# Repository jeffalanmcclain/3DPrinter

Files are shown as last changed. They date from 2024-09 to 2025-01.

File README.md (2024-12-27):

The purpose of this GIT is to serve as a CONFIG file backup for my various 3D Printers and to document the MODs I've made to them.
# [Config files](Config/README.md)
- [Flash Forge Adventurer 5M Pro](Config/FlashForge%20Adventurer%205MPro/)
- [Siboor AWD Trident 350mm](Config/Siboor%20AWD%20Trident%20350mm/)
# [Builds/Mods](Hardware/)
- Flash Forge 5MPro
- [Siboor AWD CNC Trident 350mm](Hardware/Siboor%20AWD%20Trident%20350mm/)
# [Documents/Checklists](Documents/readme.md)

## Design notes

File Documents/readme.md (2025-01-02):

# List of things to do
- [x]Install umbilical
- [x]Fix adapter cable GND/Vin swapped
- [x]Make up new umbilical from frame to toolhead
- [x]Look into X-axis resonance
 - [x]Is it affected by putting printer on hardwood floor instead of shakey card table...some, but not the double issue.
 - [x]Need better cable swing support?  Don't think so.
 - [x]Get both EBB36 adxl345 and Carto working to compare.  Now I have even MORE questions...lol.
- [x]Design webcam mount integrated into Apex-eng corner bracket
 - [x]print it and test it
- [x]Rerun Voron Calibration Cube
- [x]Rewrite entire HOME routine to force safer X/Y order operation (and skip if not needed)
- [x]Fix/Improve the feed between Extruder and HE on XOL toolhead
  - [x]Order Stainless 4mm OD x 2mm ID tube
  - [x]Install in XOL
- [x]Restructure entire congig section into directories and move some things under manta.cfg
- [x]Document everything on GIT
  - [x]Initial refactored GIT structure
  - [x]Samba share on CM4
  - [x]Sync GIT to samba share
  - [x]Sym-link Siboor config in GIT structure to ~/printer_data/config
  - [x]Pull-sync to printer
  - [x]Ensure restart works
  - [x]Update links/images formatting into better table structure
- [x]Update Internal Spoolholder STL to have recessed spring/bolts
- [x]Work on reverse tunnel proxy service to gain external access
- [x]Install Fluidd/Mainsail as docker on NAS
- [ ]Update Carto FW when available to fix Coil Frequency error
- [ ]Build StealthBurner
- [ ]Put endstop switch on Z-axis max?

# Debug Stuff for TTC and canbus traffic

- To check for errors on canbus (non-invasive)

```
candump can0,0~0,#FFFFFFFF
```

- To generate canbus loading (kills klipper, if it is running)

```
cangen -e -g 0.12 can0
```

- To watch for traffic on the canbus

```
watch -n 1 -d "ip -details -statistics link show can0"
watch -n 1 "tc -s qdisc show dev can0"
```

- To watch load on the canbus (as percentage %)

```
canbusload can0@1000000 -b -c
```

- To graph klipper.log

```
~/klipper/scripts/graphstats.py /tmp/klippy.log -o loadgraph_host.png
```

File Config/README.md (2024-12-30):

# Klipper Configs
## Methodology
Overall, I work hard to segregate things out into their individual constituant components.  Very much like Object Oriented programming, things should all be self contained inside their own entity.  This makes it (in theory) __very__ easy to remove something from your system and ONLY comment out that include file.  If you can not, then you have something wrong in your hierachy thinking.  I've done a LOT to try to enable this to function and NOT refer to other MCU pins that are NOT defined in your section.  It could be argued that some macros belong in more generalized areas, but if it deals with movement of the heads or moving the table/bed up/down, I believe THAT particular function belongs in `motion.cfg`.  
__All__ of the pin definitions for a given MCU should be in that area.  For example, there is an EBB36 MCU on the XOL toolhead.  All of the fans connected to that toolhead should be defined in there, of another file included from there like `xol_fans.cfg`.

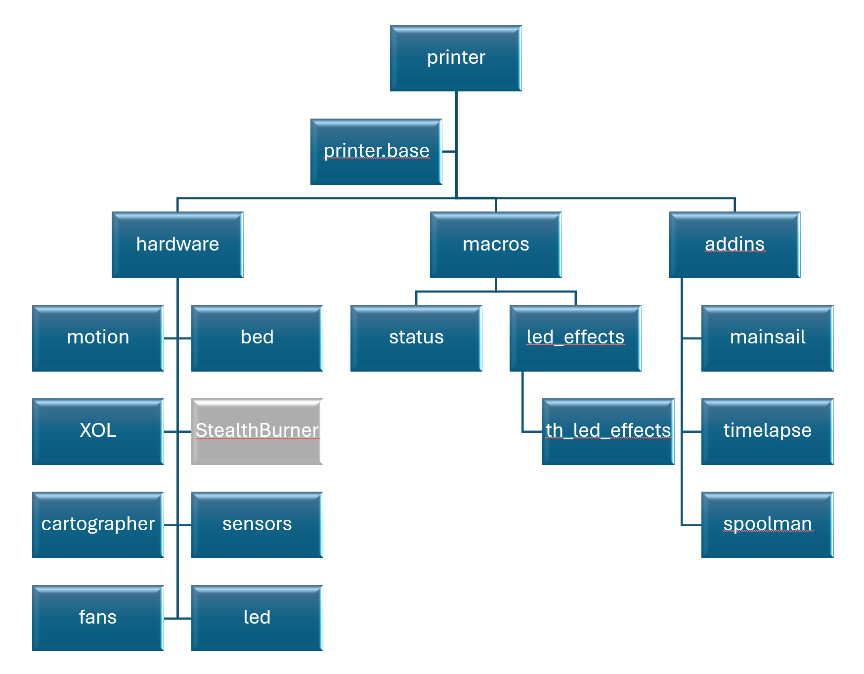
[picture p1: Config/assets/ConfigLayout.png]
Example Hierarchy of Config files


You could argue that putting toolhead fans in the `xol.cfg` breaks the idea of a "universal" fans location in the `fans.cfg` and probalby you'd be right (and even toolhead led's are in the xol.cfg, but the chamber led's are in their own led.cfg).  Technically, I should have made a `manta.cfg` under `hardware.cfg` and then put `motion.cfg` and `fans.cfg` and `bed.cfg` all below that, and you could then have fans and led below XOL as well to be more clear.  Here, each item in :red_circle:red:red_circle: has it's own MCU on the canbus.  

To that end, I have moved all my configs toward this later approach:

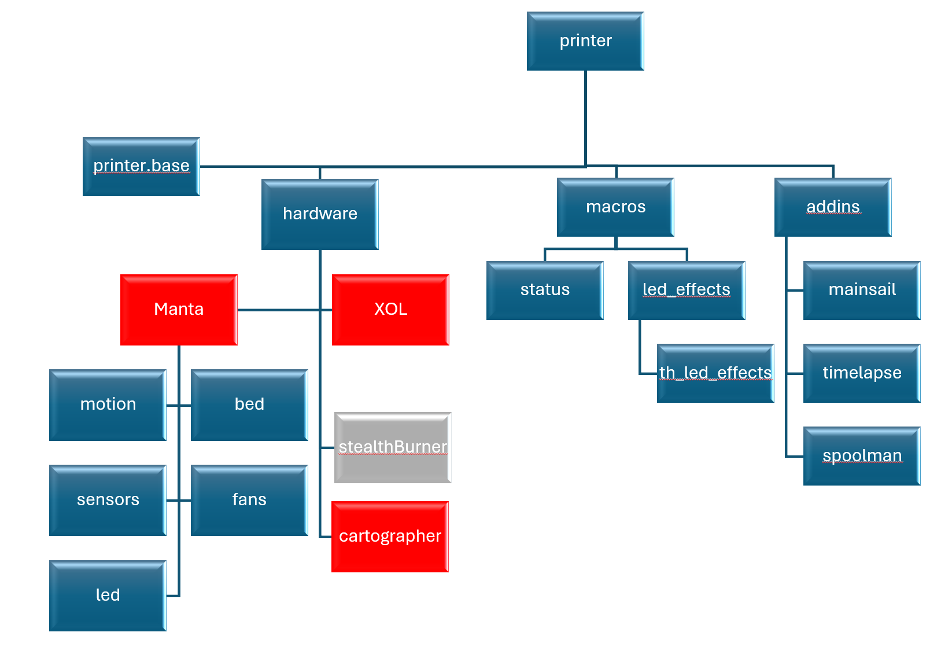
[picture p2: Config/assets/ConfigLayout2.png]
Alternate Example Hierarch


But as it stands now, to swap between StealthBurner and XOL toolhead, even with all the different toolhead MCU boards, IOs, different fans and pin defs and stuff, it is as simple as comment __OUT__ `XOL.cfg` and uncomment `stealthburner.cfg` in `hardware.cfg` include list.  Or really, to power up the printer and have it functional, without the TOOLHEAD MCU connected or even on the printer.  And all of the `[input shapper]` and hotend PID heater tunes go in each toolhead config.  NOT in `printer.cfg`.

I also have managed to REDEFINE sections (like x `endstop_pin:`) that will change once you get to the toolhead include, but the motion.cfg needs a valid PIN before (or if there is no) toolhead.cfg.  For example, I define a dummy entry for x `endstop_pin: PF4` in the manta board before it even knows about a toolhead MCU that the REAL x `endstop_pin: THB:PB6` will be connected to, and then REDEFINE this in the xol.cfg IF it is included.  

> [!CAUTION]
> This REQUIRES that I'm VERY careful not to HOME and only issue SET_KINEMATIC_POSITION to allow manual movements to be unlocked but does allow me to move my bed up/down and gantry around even without the XOL toolhead plugged in or on.

Example
**motion.cfg**
```
[stepper_x]
step_pin: PE6                         	# X-axis motor pulse pin setting
dir_pin: !PE5                         	# X-axis motor direction pin setting
enable_pin: !PC14                     	# X-axis motor enable pin setting
microsteps: 32                        	# Motor microsteps setting
rotation_distance: 40                 	# Active pulley circumference mm (2GT-20T pulley 40, 2GT-16T pulley 32)
full_steps_per_rotation: 200          	# Number of pulses required for a single motor revolution (1.8 degree motor: 200, 0.9 degree motor: 400)
endstop_pin: PF4						# Use Manta Endstop 0 dummy for now when no TH plugged in
...
```

**xol.cfg**
```
[extruder]
step_pin: THB:PD0                 		# Step pin
dir_pin: !THB:PD1                 		# Direction pin, "!" indicates logic inversion
enable_pin: !THB:PD2              		# Enable pin, "!" indicates logic inversion
full_steps_per_rotation: 200         	# Number of pulses required for a single motor revolution (1.8 degree motor: 200, 0.9 degree motor: 400)
microsteps: 16                       	# Microsteps setting
gear_ratio: 9:1                      	# Gear ratio
...

# Redefine the X-motion endstop_pin!
[stepper_x]
endstop_pin: THB:PB6                  	# Limit switch PIN setting (X-)
```

## The Repos
- [FlashForge Adventurer 5MPro](FlashForge%20Adventurer%205MPro)

- [Siboor AWD Trident 350mm](Siboor%20AWD%20Trident%20350mm)

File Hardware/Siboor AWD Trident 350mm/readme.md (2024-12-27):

This will document the build and MODS to my [Siboor AWD Trident 350mm](https://www.siboor.com/product/siboor-voron-trident/)
# The [Hardware Build](Build.md)
# Hardware [upgrades/MODs](MODs.md)
# Software [upgrades/MODs](Software.md)

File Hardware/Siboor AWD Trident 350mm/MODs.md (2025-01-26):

# Hardware upgrades/MODs
These are the MODs I've made to my [Siboor AWD Trident 350mm](https://www.siboor.com/product/siboor-voron-trident/)

First, a couple tips/hints/suggestions if I were going to do it over:
1. Do NOT route your USB cables in the electronics bay wire loom channels.  It makes it nice and tidy, but these are likely to change and it is supper hard to pull them back out later.
2. I would pre-grind the AWD Al mounting brackets a bit, to increase the clearance between them and the 2020 extrusions to allow more easily to slip USB cabling and other motor wiring (and yes, even the Canbus cable) to fit there.  It is a real pain to try to pull them out and fit them back in there later.
3. Try to use the dedicated JST-XH or whatever 4-pin USB port on the main board for at least one USB webcam.  Just chop off the end of the cable and wire it up with the wire ends included in the Siboor kit.

| Item| Description | Rating | Images |
|	---	|	---	| ---	|	---	|
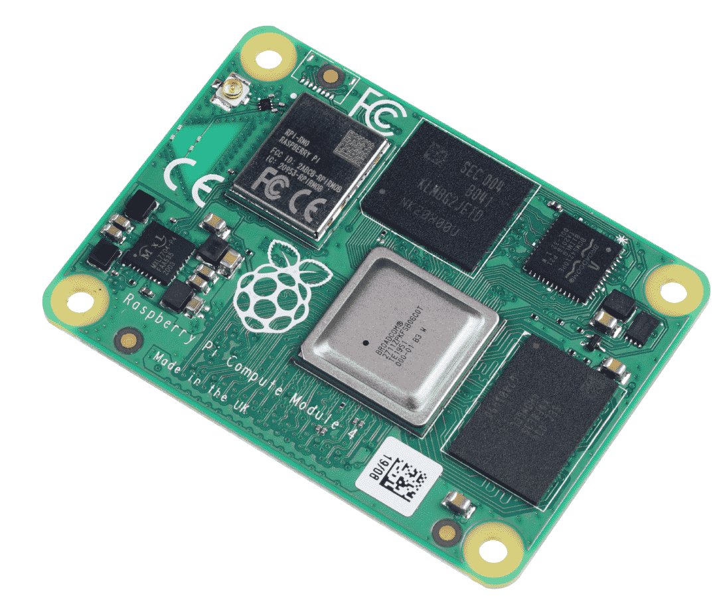
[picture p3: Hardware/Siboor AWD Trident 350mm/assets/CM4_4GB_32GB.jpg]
CM4 4GB/32GB
| [CM4 4GB/32GB](https://www.seeedstudio.com/Raspberry-Pi-Compute-Module-CM4104032-p-4722.html) | Got this to try to avoid all the Timer Too Close MCU fails and have enough resources to manage two webcams and have more onboard storage than the CB2 offering. So far, once I eliminated the [LED Effects](https://github.com/julianschill/klipper-led_effect) plug-in module, which was causing massive TTC failures on both the Manta MCU and EBB36 MCU, it has handled everything like a champ. | :star::star::star::star: |   |
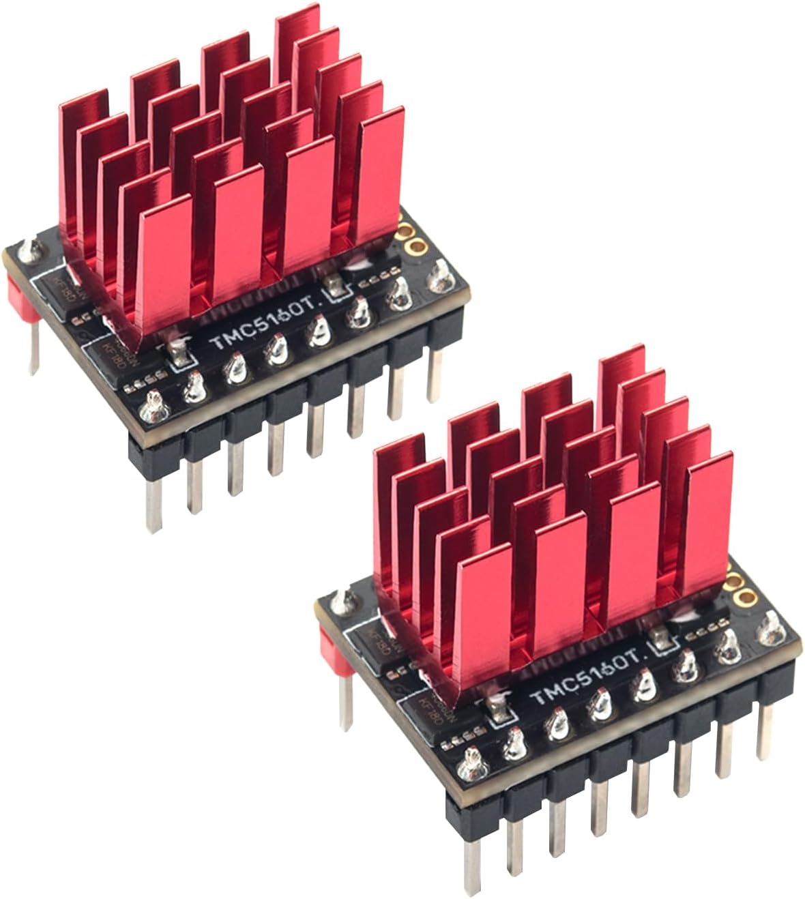
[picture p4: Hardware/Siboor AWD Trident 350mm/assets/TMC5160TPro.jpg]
TMC5160Pro drivers
| [TMC5160T Pro drivers](https://www.amazon.com/BIGTREETECH-TMC5160T-High-Speed-Printing-Heatsink/dp/B09JS5YDQN/ref=sr_1_2) | Really good higher power drivers to support 48v | :star::star::star::star: |   |
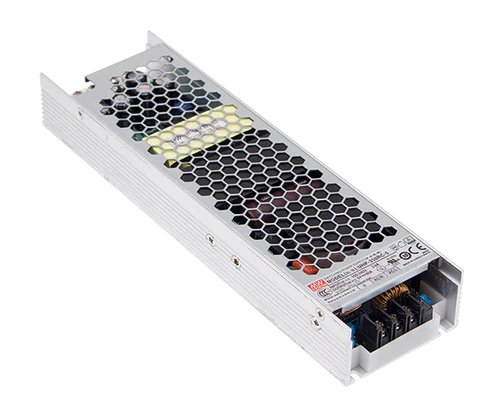
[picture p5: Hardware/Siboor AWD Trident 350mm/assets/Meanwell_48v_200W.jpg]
Meanwell 200W 48V PSU
| [48v 200W PSU](https://west3d.com/products/mean-well-uhp-200-48-200w-48v-4-2a-power-supply-psu-1?_pos=1&_sid=3af408982&_ss=r) | HV supply for X/Y motors to run at 48v | :star::star::star::star: |  |
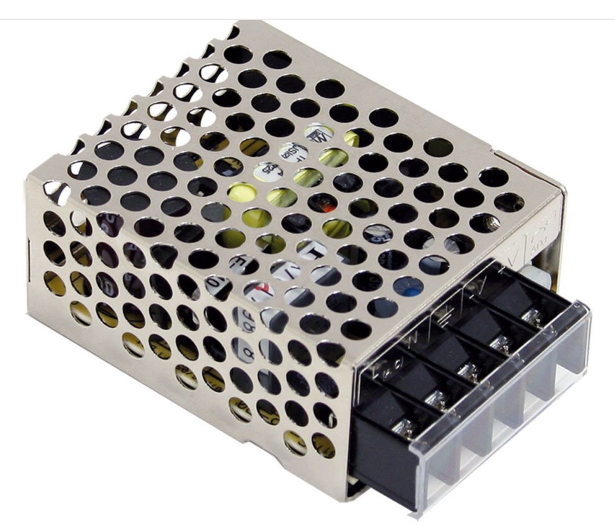
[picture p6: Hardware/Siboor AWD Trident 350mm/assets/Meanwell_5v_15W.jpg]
Meanwell 15W 5V PSU
| [5v 15W PSU](https://www.amazon.com/gp/product/B005T6UJBU/ref=ppx_yo_dt_b_search_asin_title?ie=UTF8&psc=1) | Simple PSU for dedicated supply to chamber LEDs and a powered USB hub. Probably needed a little more than just 15W out of this to get better rating. | :star::star::star: |  |
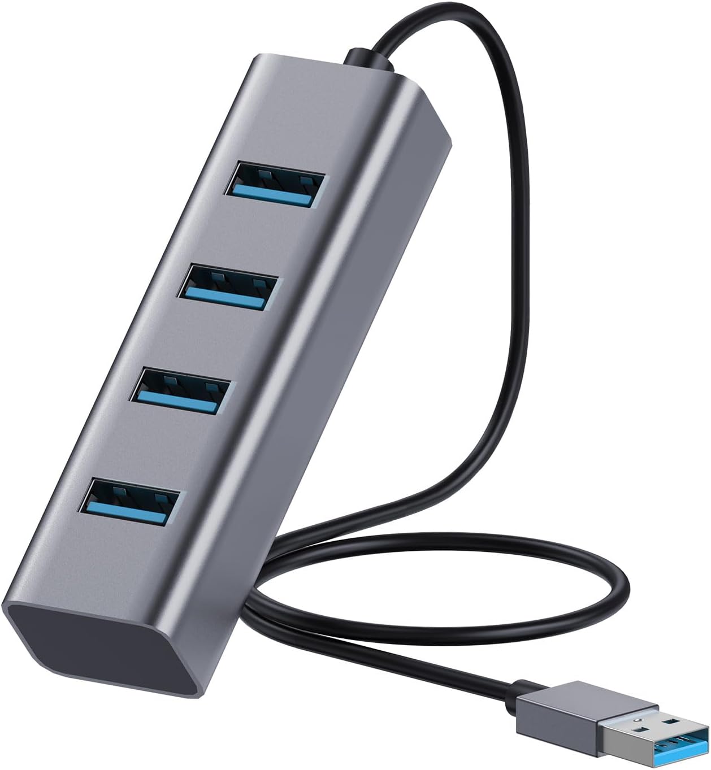
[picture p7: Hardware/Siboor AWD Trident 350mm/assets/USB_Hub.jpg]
USB hub
| [USB hub](https://www.amazon.com/dp/B0CWNPTH8F?ref=ppx_yo2ov_dt_b_fed_asin_title) | Simple and small hub expansion. Wish it was powered (may hack it to add in 5V supply).  And, after fighting with my two USB webcams, it makes sense that you can't just run them on a hub and expect USB 2.0 bandwidth to be able to be "split" for the additional stream.  Luckily, I figured out that the Manta M8p v2 has 3x USB 2.0 ports.  Just one of them is a dedicated plug (not USB A) on the motherboard.  So, I'm going to wire this HUB into that and let the webcams play on their own ports. | :star::star::star: |  |
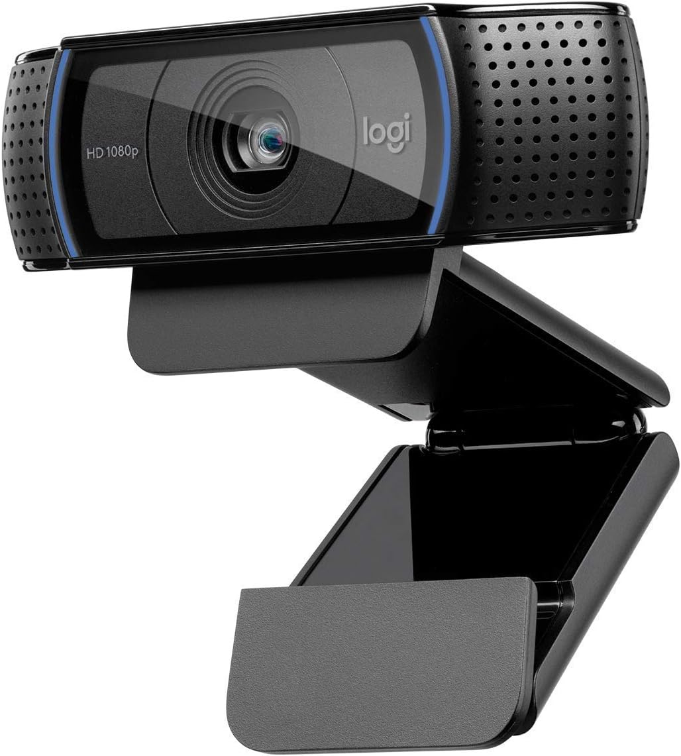
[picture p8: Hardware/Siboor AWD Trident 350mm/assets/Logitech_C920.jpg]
Logitech C920
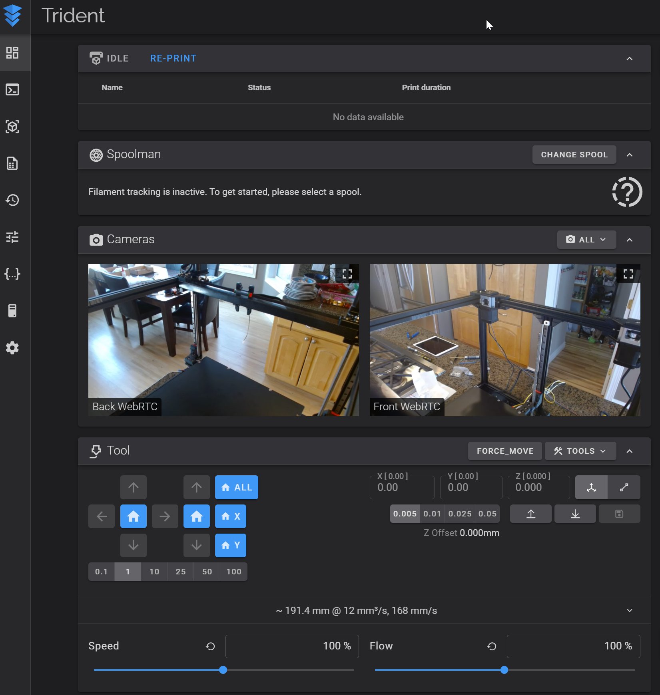
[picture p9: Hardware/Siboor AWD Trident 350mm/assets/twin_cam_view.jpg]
Twin Cam View
| [Logitech C920](https://www.amazon.com/dp/B085TFF7M1?ref=ppx_yo2ov_dt_b_fed_asin_title&th=1) (x2) | Specs: 1080p/30fps and 78' FoV.  This really needs more like 100' FoV and fixed focus and it would be better, but color and low light works well. | :star::star: |   |
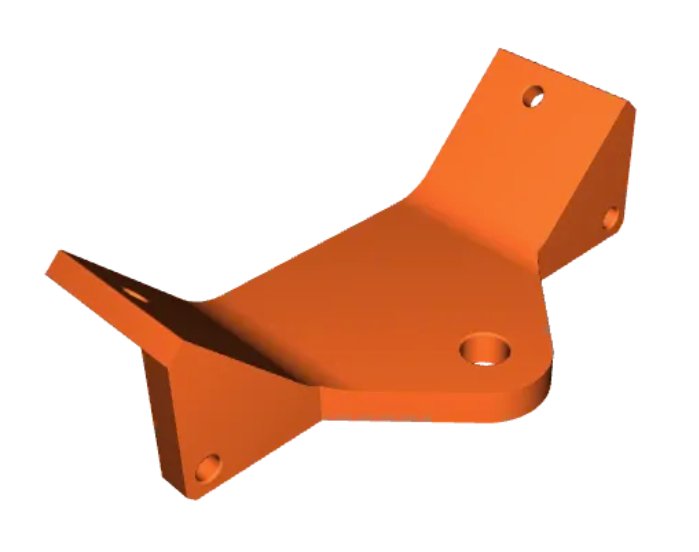
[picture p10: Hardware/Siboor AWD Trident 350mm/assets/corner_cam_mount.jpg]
USB Cam Corner mount
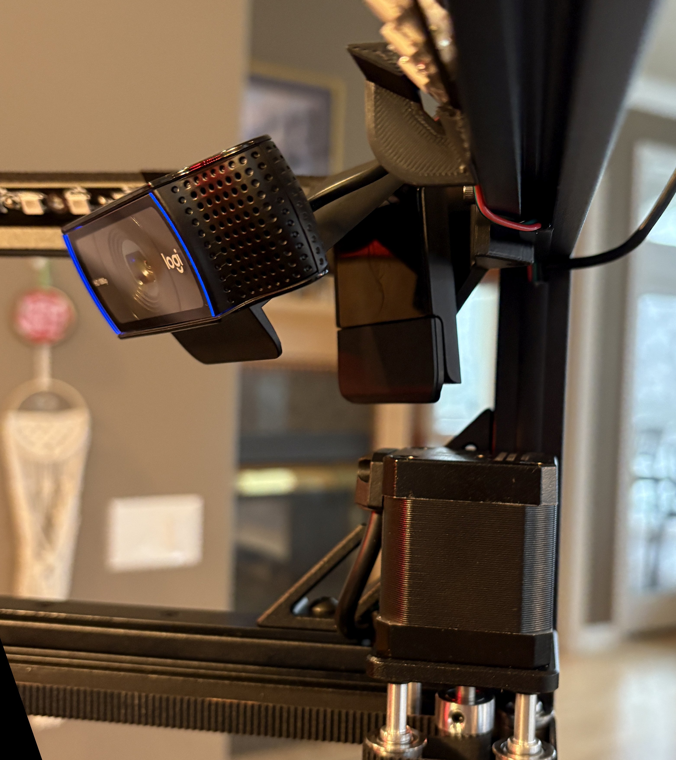
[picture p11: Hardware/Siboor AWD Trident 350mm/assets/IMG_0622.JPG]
| [Printables Corner Mount STL](https://www.printables.com/model/1101887-logitech-c920-2020-corner-mount) | 2020 Extrusion corner mount for Logitech C920 I designed | :star::star::star::star: |   |
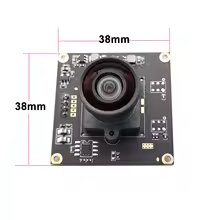
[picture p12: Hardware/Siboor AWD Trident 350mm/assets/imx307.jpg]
IMX307
| [IMX307 1080p bare camera](https://www.aliexpress.us/item/3256806095943563.html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) (x2) | Specs: 1080p/60fps and 100' FoV.  This bare bones 38mmx38mm board without any autofocus and a wider FoV was latest pick for chamber webcam. | :star::star::star: |  |
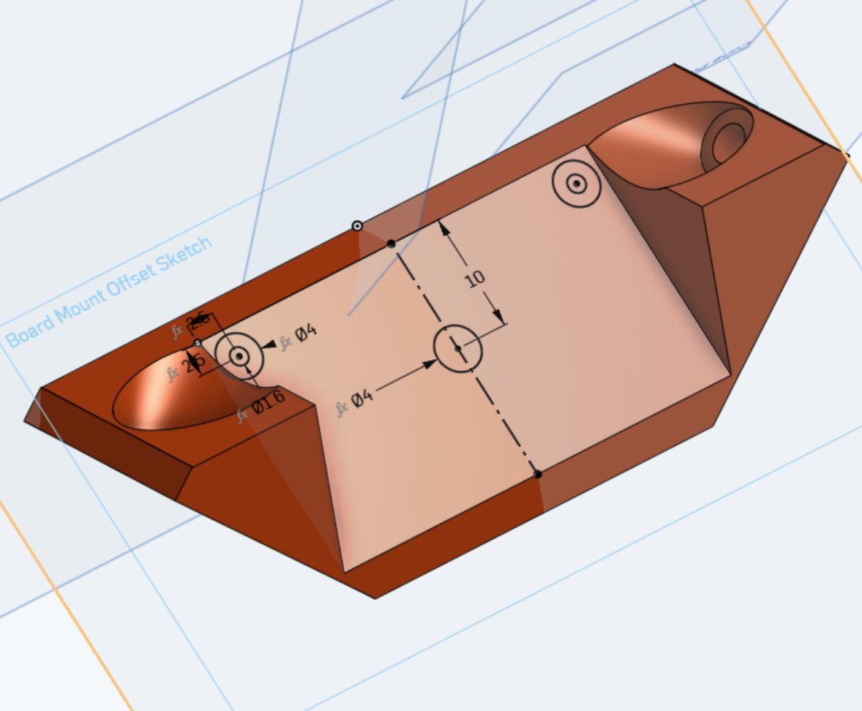
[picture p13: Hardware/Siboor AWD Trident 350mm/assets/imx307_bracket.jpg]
IMX307 Corner mount
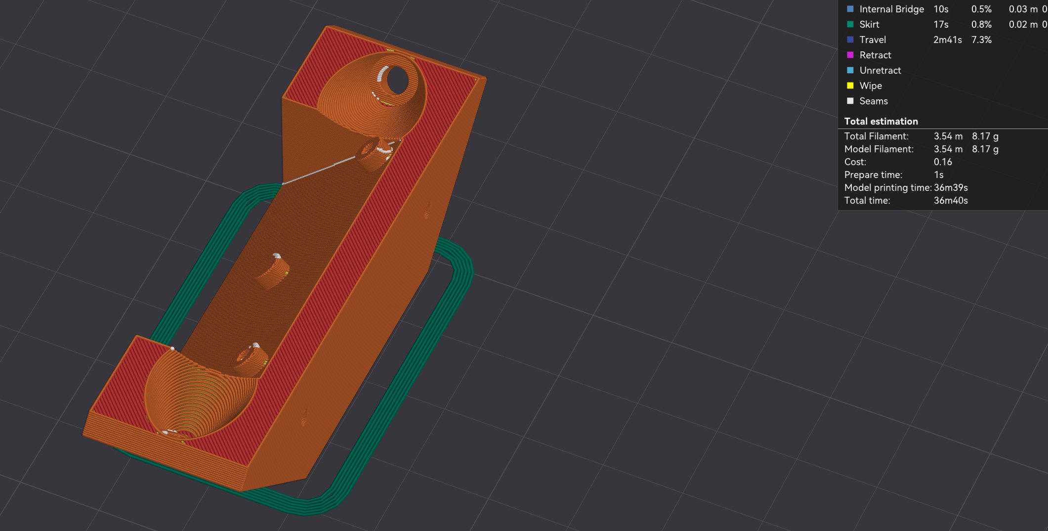
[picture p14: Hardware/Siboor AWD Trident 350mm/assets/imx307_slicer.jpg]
| [Printables 2020 Corner Mount for IMX307](https://www.printables.com/model/1160911-imx307-bare-board-webcam-2020-corner-mount) | 2020 Extrusion corner mount for IMX307 bare board with 45' down-tilt, which I designed | :star::star::star::star: |   |
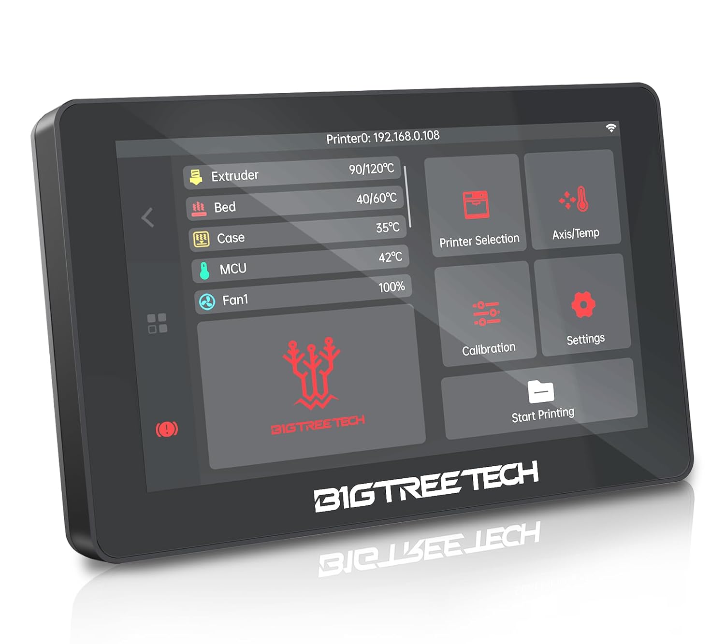
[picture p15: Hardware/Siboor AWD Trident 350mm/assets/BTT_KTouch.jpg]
BTT K-Touch wireless screen
| [BTT K-Touch wireless screen](https://www.amazon.com/dp/B0D4YTSLDZ?ref=ppx_yo2ov_dt_b_fed_asin_title) | Wireless battery powered display works, but needs better firmware support to add more features more like KlipperScreen. I got it on black Friday sale, and it "works" but just waiting for them to maybe improve the firmware. | :star::star: |  |
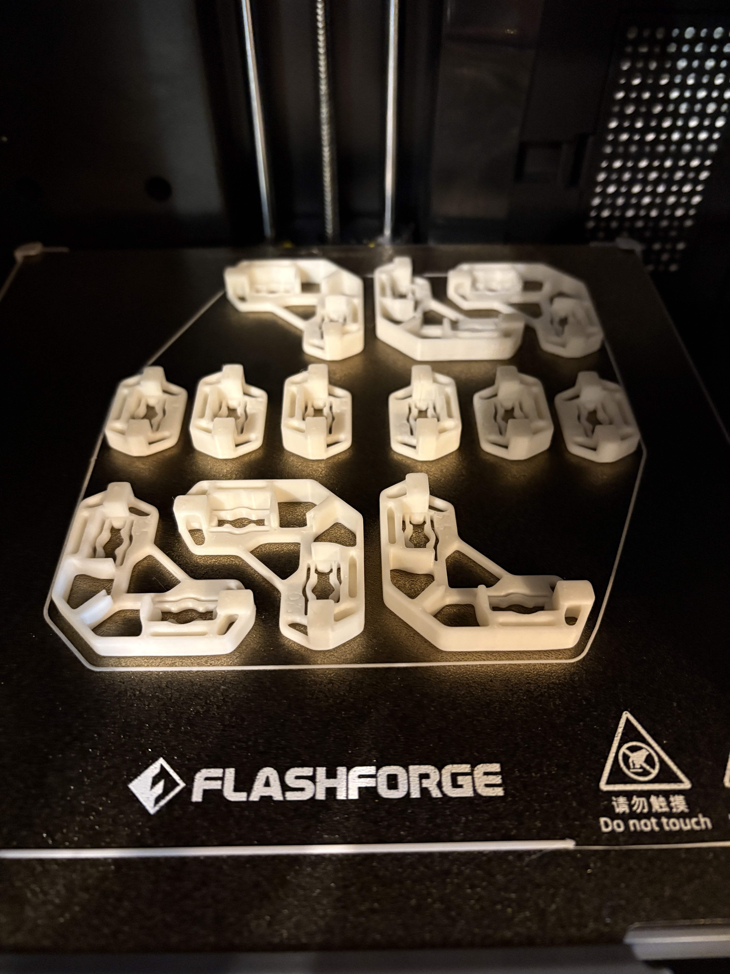
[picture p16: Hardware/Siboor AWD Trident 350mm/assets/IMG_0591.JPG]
Annex-Eng panel clips
| [Annex-Eng panel clips](https://github.com/Annex-Engineering/Annex-Engineering_User_Mods/tree/main/Printers/All_Printers/annex_dev-Panel_2020_Clips_and_Hinges) | **Top & Back** panel using 5.0mm with 3mm foam tape (use 3.5mm clips for back if using stock 1mm foam).  **Side** panels using 5.5mm clips with 3mm foam | :star::star::star::star::star: |  Annex-Eng panel clips   |
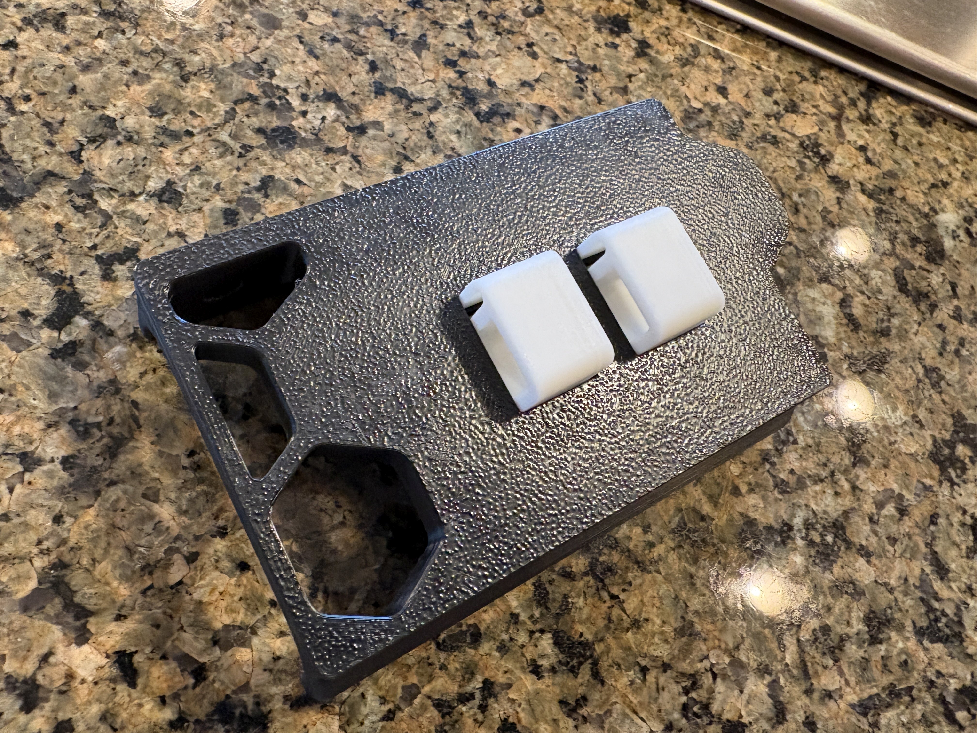
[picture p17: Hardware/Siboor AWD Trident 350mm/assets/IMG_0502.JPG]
keystone slots
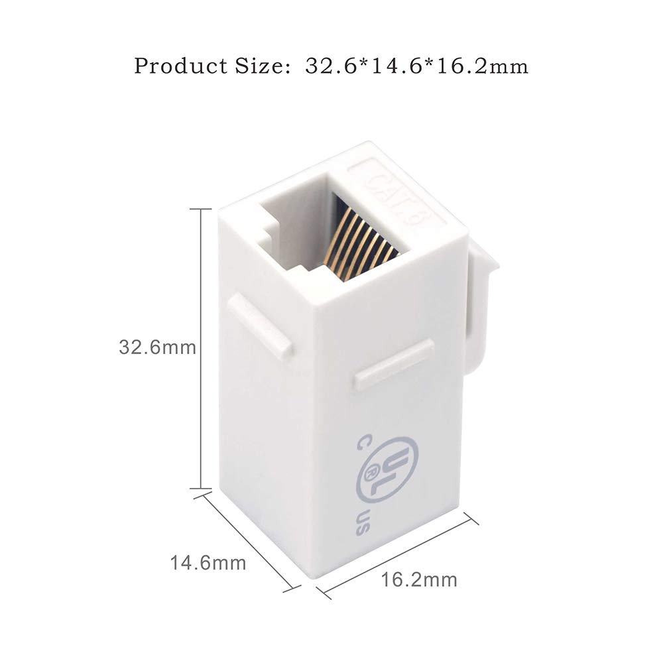
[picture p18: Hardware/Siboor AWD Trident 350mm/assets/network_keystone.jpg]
Network keystone
| [Network keystone](https://www.amazon.com/dp/B0116T7XMQ?ref=ppx_yo2ov_dt_b_fed_asin_title&th=1) | Doesn't fit in printed square slot great, but I think that is a problem with skirt model | :star::star::star::star: |   |
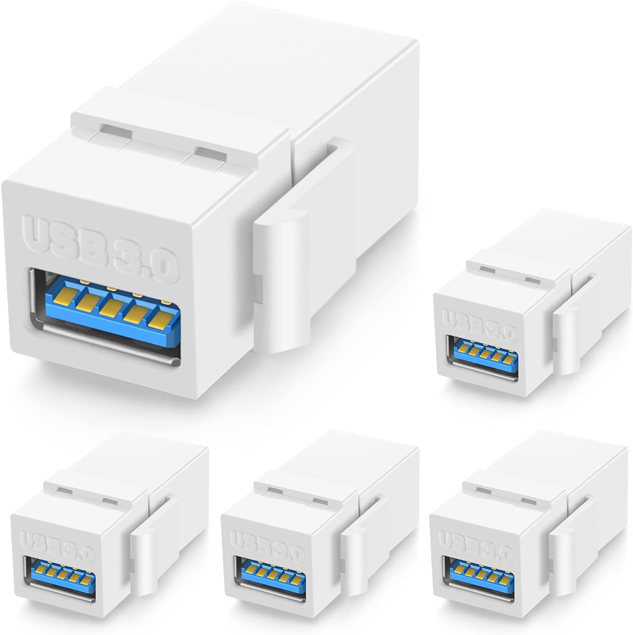
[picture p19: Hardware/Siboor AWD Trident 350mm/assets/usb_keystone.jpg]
USB keystones
| [USB keystones](https://www.amazon.com/dp/B078935SFG?ref=ppx_yo2ov_dt_b_fed_asin_title&th=1) | Doesn't fit in printed square slot great, but I think that is a problem with skirt model | :star::star::star::star: |  |
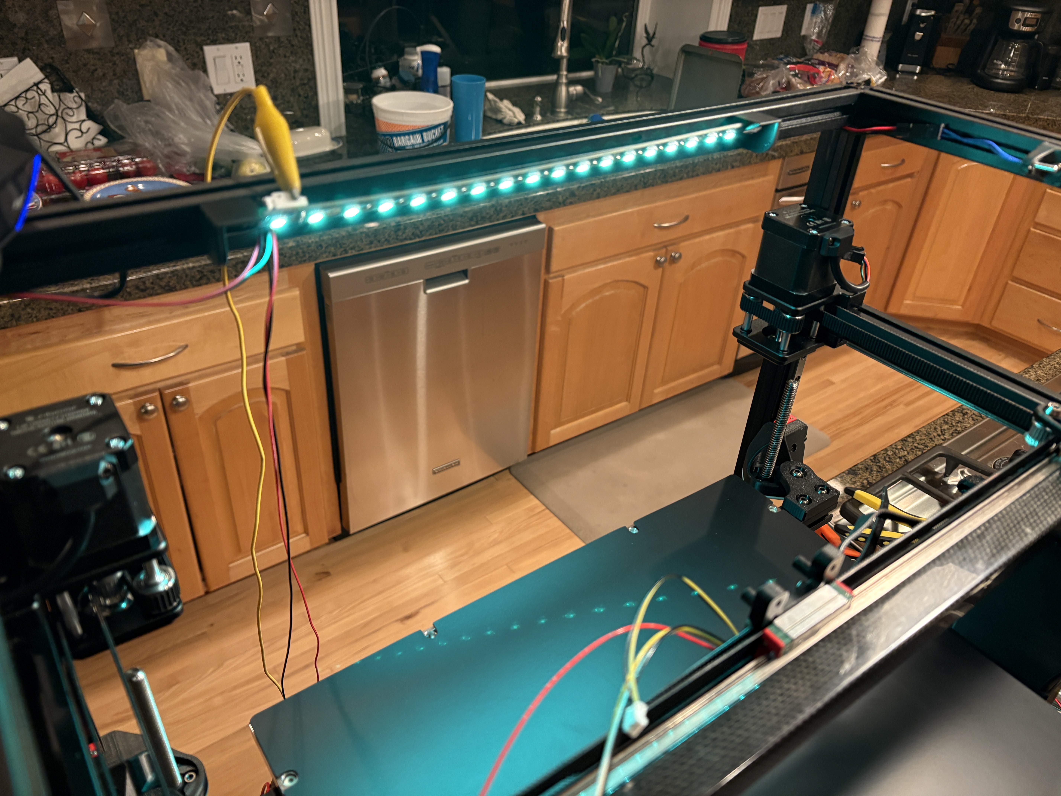
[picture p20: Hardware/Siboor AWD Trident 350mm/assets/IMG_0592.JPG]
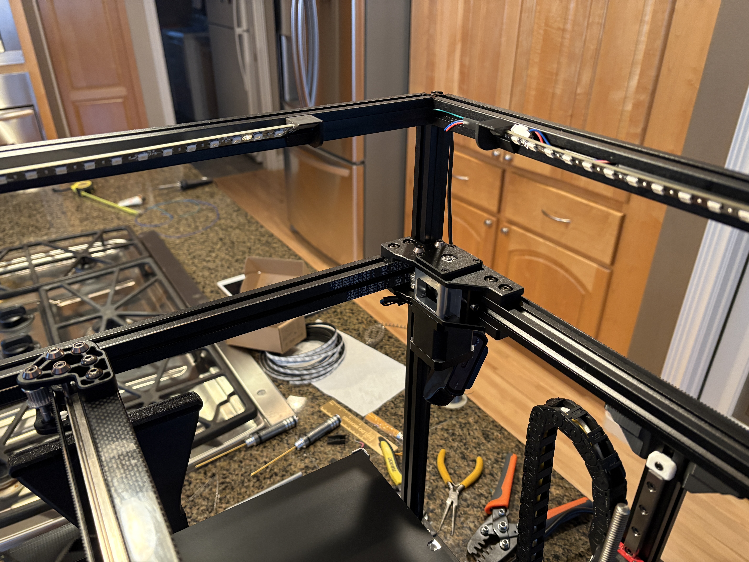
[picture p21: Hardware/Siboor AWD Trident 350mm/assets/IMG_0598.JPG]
| [270mm Disco LED sticks](https://www.siboor.com/product/voron-2-4-v2-4-3d-printer-daylight-disco-on-a-stick-pcb-kits-5v-lamp-bar-270-158mm-for-voron-0-1-0-2-2-4-trident-350-300-250mm/) (x4) | 270mm WS2812B 5v 18-LED light bar. Needs VCC/GND solder pads at other end too | :star::star::star: |   |
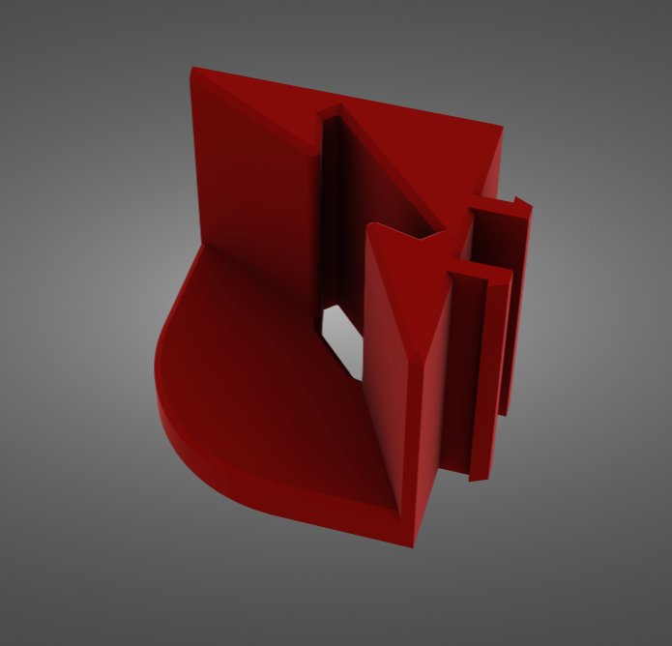
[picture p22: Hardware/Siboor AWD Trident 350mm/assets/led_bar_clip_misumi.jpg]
| [LED Bar Clip Misumi v2](https://github.com/VoronDesign/VoronUsers/blob/main/printer_mods/eddie/LED_Bar_Clip/LED_Bar_Clip_Misumi_version2.stl) | Need to size up 10% to fit the Disco LEDs I got and to fit snug in 2020 extrusion. Also, slot makes it difficult to fit pass on wiring through. | :star::star::star: |  |
| Rear motor flip | Easy to do, and required for XOL toolhead clearance | :star::star::star: | Rear Motor flip |
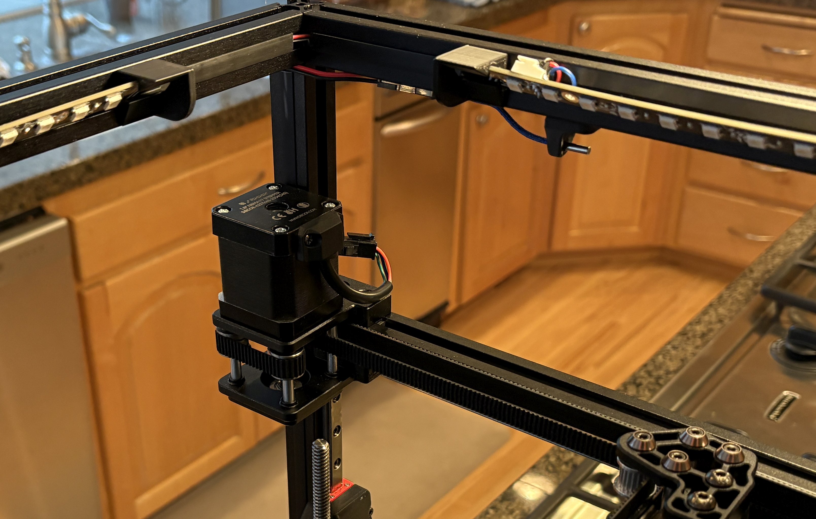
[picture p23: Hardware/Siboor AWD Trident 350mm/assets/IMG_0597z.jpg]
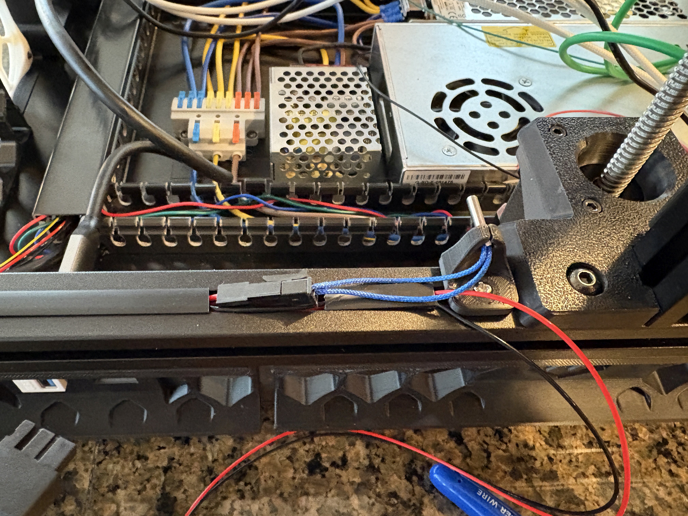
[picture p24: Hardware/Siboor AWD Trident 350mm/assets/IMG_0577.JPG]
| Additional Temp sensors | One at **TOP** of chamber and one at **Bottom** plus x1 in electronics bay near drivers. | :star::star::star::star: |   Temp Sensor |
| [Thermistor 2020 mount](https://mods.vorondesign.com/details/dfRX88k7wwS6tpYlvyCEw) | great 3mm t-nut mount for thermistor.  Might be a little bulkier than necessary. | :star::star::star::star: | 2020 Temp Sensor mount |
| [Digital Humidity Sensor](https://www.amazon.com/gp/product/B0CXHS6CYS/ref=ppx_yo_dt_b_search_asin_title) | Good digital temp/humidity sensors for your filament storage boxes and for a low tech quick chamber temp/humidty reading. | :star::star::star::star: | Digital Thermometer |
| [Digital Humidity Sensor 2020 Mount](https://www.printables.com/model/1113476-temp-humidity-sensor-2020-bracket) | Mount for common digital thermomenter/hygrometer I designed. | :star::star::star::star: | Digital Thermometer mount Digital Thermometer mount |
| [XOL toolhead](https://github.com/Armchair-Heavy-Industries/Xol-Toolhead) | Ugly, but light and very functional print head with lots of extruder/hotend support. I would like a little more powerful fans (may need to look into higher RPM Delta fans) | :star::star::star::star: | XOL + EBB36 + G2SA |
| [Rapido2 UHF PT1000](https://www.phaetus.com/products/rapido2?variant=45177211060501) Hotend | Great Ultra High Flow with 0.4mm and 0.6mm Hardened nozzles | :star::star::star::star: | Rapido2 UHF PT1000 |
| [EBB36 Toolhead Board](https://github.com/bigtreetech/EBB) | Pretty typical board for this toolhead. Documentation could have been more clear and better, especially for PT1000 sensor pins. I **also** am frustrated that the included PT1000 secondary sensor doesn't work if using the main one. | :star::star::star::star: | EBB36 Wiring |
| [Galileo 2 Stand Alone](https://github.com/JaredC01/Galileo2/tree/main/galileo2_standalone) Extruder | Really happy with this large extruder. Pulls hard and single gear with idler design, so should avoid some of the binding extrusion artifacts | :star::star::star::star: | G2SA |
| [Stainless Steel 4mmOD / 2mmID capilary tube](https://www.amazon.com/dp/B0C5QZ28F2?ref=ppx_yo2ov_dt_b_fed_asin_title&th=1) | I was having problems with the 2mmID PTFE tube in the toolhead between the extruder and the Rapido2.  I had originally a 32.6mm PTFE length section though the XOL build site didn't have Galileo2 to Rapido2 measurement, they said 43mm for Rapido/Orbiter2.0.  I test fit longer ones and trimmed to have it just fit and 35mm seemed to fit.  Cut some stainless steel tubing (4mmOD/2mmID) to 34.78mm and drilled it out to 2mm, just to deburr it.  Lightly reamed out the opening on the extruder side to help funnel filament in.  Got it to feed in fine (better than the PTFE), so now just see how it does longer term.  Likely the shorter than needed PTFE tube was the reason it got damaged and hung up to begin with.  Test fitting originally, that was as long as I could get, but sounds like the ASA print tapers a bit and probalby I wasn't as far up as I needed.  Unfortunate that there wasn't a good PTFE length on [the XOL GIT table](https://github.com/Armchair-Heavy-Industries/Xol-Toolhead/blob/main/docs/PTFE_Length.md).  I need to conduct some tests to see if it is possible to get melted filament stuck in the SS tube compared to PTFE (likely PLA or TPU will be worst and trying to back out an appreciable amount to sit in the SS tube quickly and cool that way).  *Update* well, filament doesn't seem to "stick" to the stainless however, you CAN get a balled up filament end that doesn't pull out through the stainless 2mm hole and WON'T go back into the hotend to melt if you mess around too much moving it in/out of the cool stainless.  LoL.  Also, I have found that the 43mm *is* closer to reality.  You just have to shove the tube REALLY HARD.  The layer lines sort of keep it from sliding all the way in/up but if you push it pretty good, you can get all of 42.3mm in there and THAT seems to do much better at not getting stuck (likely because it doesn't have a big gap now... | :star::star::star::star: | Stainless Steel capilary tube XOL toolhead tubing Stainless Steel capilary tube |
| [XOL EBB36 + G2SA drag chain mount](https://www.printables.com/model/794851-xol-horizontal-drag-chain-ebb36-for-g2sa) | Needed some modification to fit my chain plus, it needed to sit higher on the toolhead. | :star::star::star: | Drag chain mount to EBB36 |
| Cartographer mounts | Printed 4.5mm spacers for the bottom to setup the cartographer with proper 2.5mm-3.0mm spacing up from nozzle. | :star::star::star: | Cartographer mount spacers |
| **Horizontal drag chain elim and move to umbilical** [PG7 2020 mount](https://www.printables.com/model/1099507-voron-trident-pg7-mount-bracket) | Good mount for the PG7 cable in the 2020 corner | :star::star::star::star: | 2020 PG7 mount |
| **Horizontal drag chain elim and move to umbilical** [EBB36 PG7 mount](https://www.printables.com/make/2268162) | Good mount for the XOL toolhead on G2SA + EBB36 board for PG7 | :star::star::star::star: | Cartographer mount spacers |
| [PTFE bend support](https://www.printables.com/make/2268145) | Keeps PTFE tube from bending/collapsing | :star::star::star: | PTFE tube support CPTFE tube support |
| [Internal Spool Holder](https://www.printables.com/model/1105610-spring-loaded-internal-spool-holder) | Spring tensioned Internal 1Kg spool holder with rollers. I need to redesign it a touch to allow spring mount bolts to be recessed because it interferes with electronics bay panel removal as it is. | :star::star::star::star:| Internal Spool Holder Internal Spool Holder |
| [Armored Turtle 4-to-1 Filament Hub with Runout Sensor](https://github.com/ArmoredTurtle/BoxTurtle/blob/main/STLs/Legacy/%5Ba%5D_hub_D2F.stl) | Works to combine up to 4 sources, I've "upgraded" to the legacy version of this hub, which has support for the more standard and available micro switch. Seems like Klipper expects your Endstop switches to be pulled logically to GND (you can't pull to VCC and just invert the logic). | :star::star::star::star: | Armored Turtle 4-to-1 Filament Hub Filament Hub |
| [Voron Strengthened X Handles](https://www.printables.com/model/1053718-strengthened-voron-x-handles) | If you want/need handles on the top to lift | :star::star::star::star: | Voron Strengthened X Handles |
| [Filament Dry Box spool holders](https://www.printables.com/model/983885-modular-minimal-filament-drybox-with-no-bearings-r) | Good hanger system for inside 4L dry cereal boxes to store filament and spool out of | :star::star::star::star: | Filament Dry Box spool holders Filament 4-to-1 hub Dry Box |

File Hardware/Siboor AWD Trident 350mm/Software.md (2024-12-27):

# Software upgrades/MODs
| Item | Description | Images |
| --- | --- | --- |
| [Raspberry Pi 64-bit Debian v12](https://www.raspberrypi.com/software/operating-systems/#raspberry-pi-os-64-bit) | Desktop version of Debian v12 bookworm | |
| [Esoterical Canbus](https://canbus.esoterical.online/) | Really, just a firmware guide for Klipper and Katapult installation | |
| [Crowsnest](https://github.com/mainsail-crew/crowsnest) | Good webcam manager plug-in for moonraker | |
| [Spoolman](https://github.com/Donkie/Spoolman) | Excellent filament spool manager database that integrates into printer to monitor usage (works in Fluidd and Mainsail) | Gantry |
| [Timelapse](https://github.com/mainsail-crew/moonraker-timelapse) | Good plugin for moonraker that allows time lapse footage per layer as well as parked head snapshots (Fluidd and Mainsail supported) | timelapse |
| Orca Slicer Custom Bedmap | Created a custom bedmap for the XOL front AWD keep out area.  I have the [custom STL](../../Config/Siboor%20AWD%20Trident%20350mm/ORCA/Custom%20Siboor%20350%20XOL%20umbilical.stl) for the bed in the config/Orca section. | Bedmap |
| [SAMBA setup Guide](https://pimylifeup.com/raspberry-pi-samba/) | Adding a SAMBA share to your CB2/CM4/RPi4 main processor makes it easy to share with windows file mounts.  I'm using this to allow me to directly edit/push/sync to GIT. | |

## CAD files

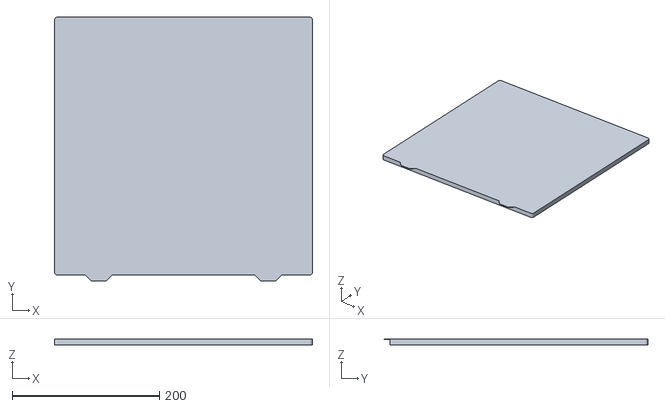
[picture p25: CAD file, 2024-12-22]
Config/Siboor AWD Trident 350mm/ORCA/Trident_JUNE_350_Printer_Bed_Mould.stl
350.0 x 358.0 x 8.75

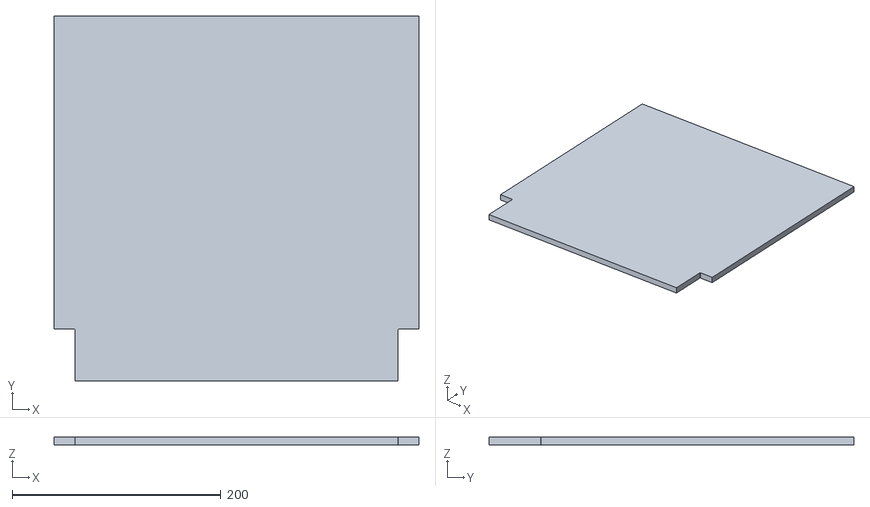
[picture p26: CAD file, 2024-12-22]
Config/Siboor AWD Trident 350mm/ORCA/0806Trident_JUNE_350__bed_Shape.stl
350.0 x 350.0 x 8.00

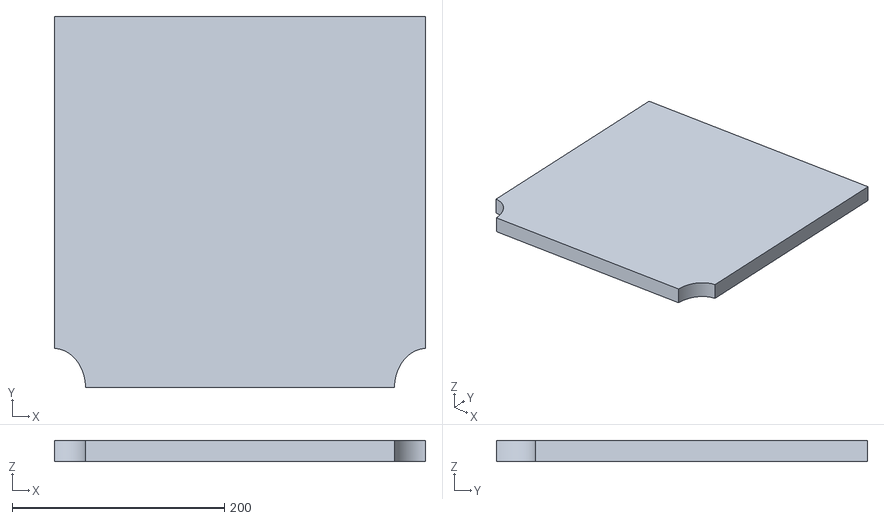
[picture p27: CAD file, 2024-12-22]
Config/Siboor AWD Trident 350mm/ORCA/Custom Siboor 350 XOL umbilical.stl
349.5 x 349.5 x 20.0

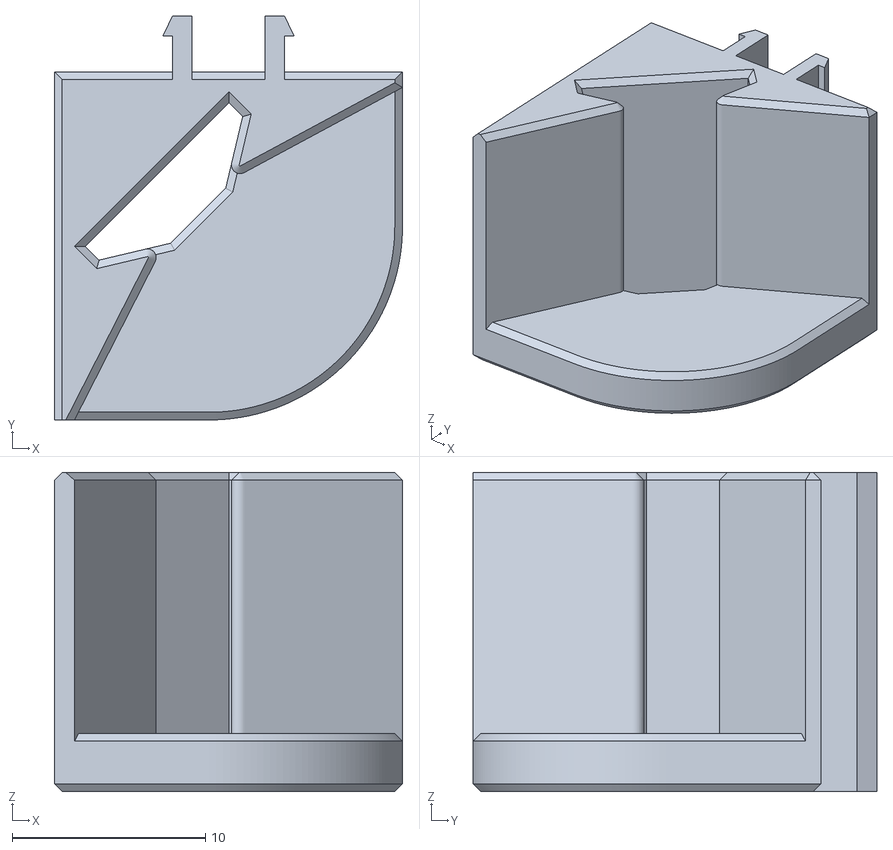
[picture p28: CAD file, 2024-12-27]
Hardware/Siboor AWD Trident 350mm/assets/LED_Bar_Clip_Misumi_version2.stl
18.0 x 20.9 x 16.5

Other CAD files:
Config/Siboor AWD Trident 350mm/ORCA/Custom Siboor 350 XOL.stl

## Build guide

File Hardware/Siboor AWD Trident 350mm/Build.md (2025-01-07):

# The Build
| Item | Description | Images |
| ---  | --- | ---|
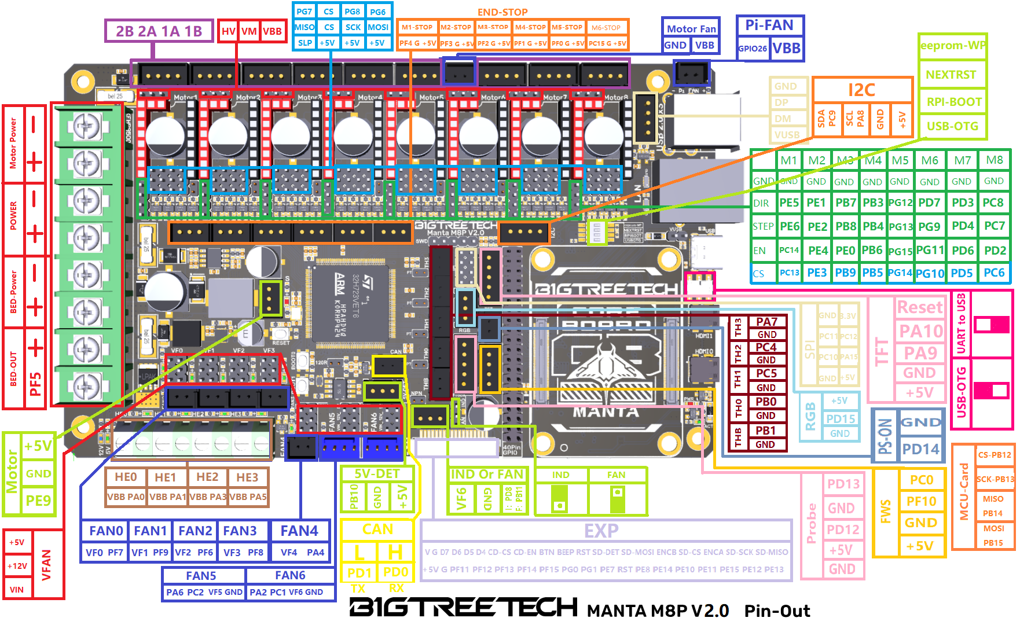
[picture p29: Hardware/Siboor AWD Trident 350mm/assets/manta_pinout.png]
Manta M8P Pin out
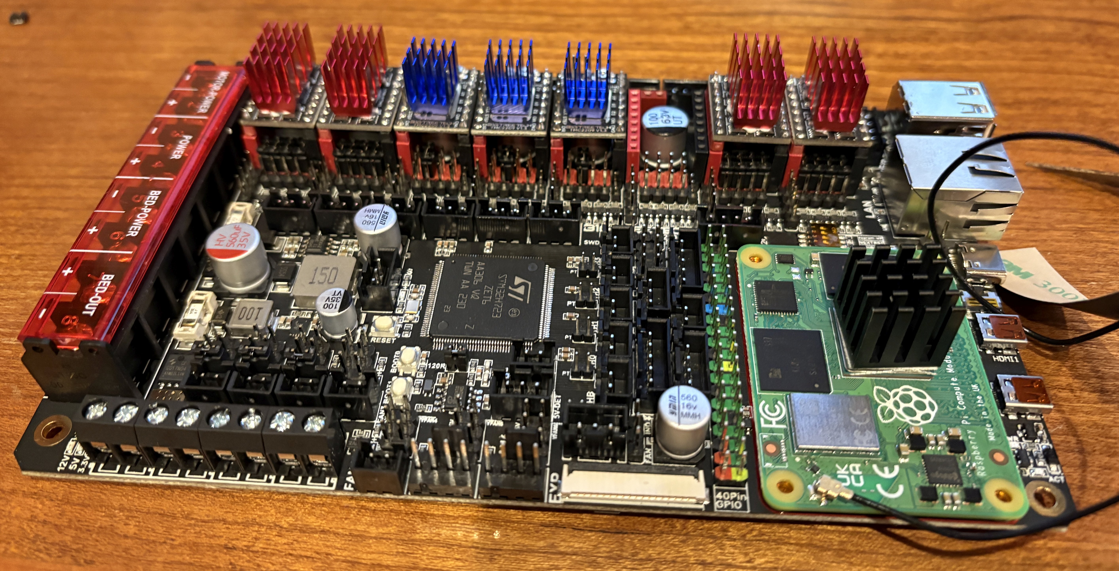
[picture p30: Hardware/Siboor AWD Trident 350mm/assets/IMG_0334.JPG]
TMC5160Pro drivers
| [Manta M8p v2](https://github.com/bigtreetech/Manta-M8P) and CM4 prep | I went ahead and flashed new OS image for the CM4 and got all the Klipper, Fluidd, Mainsail, Moonraker, Crowsnest, Spoolman stuff setup with [kiauh](https://github.com/dw-0/kiauh) script |   |
| 2020 Frame | Built the frame on a nice, flat granite counter-top and used blue loc-tite on all the extrusion screws.  Careful to measure diagonals and keep square and measure gantry and ensure parallel to bottom. | 350mm Frame |
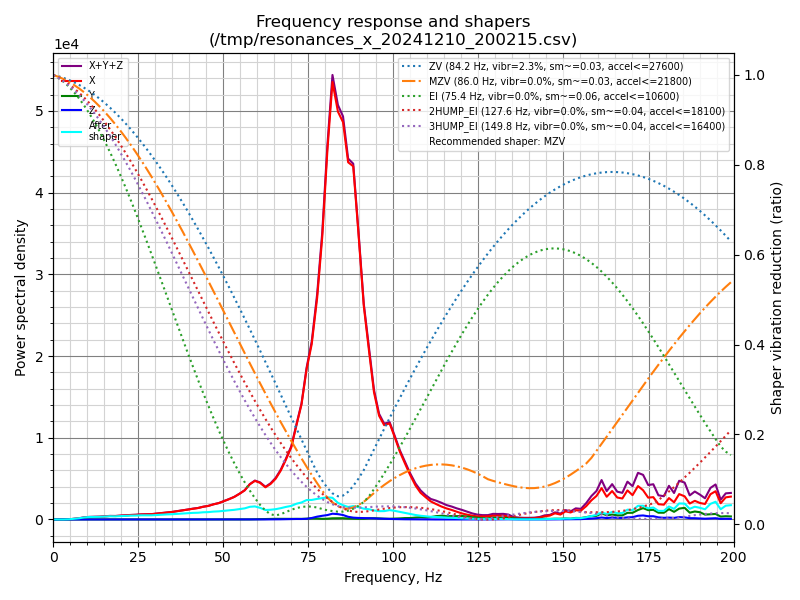
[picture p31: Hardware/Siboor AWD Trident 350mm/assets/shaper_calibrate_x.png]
X-axis Shaper
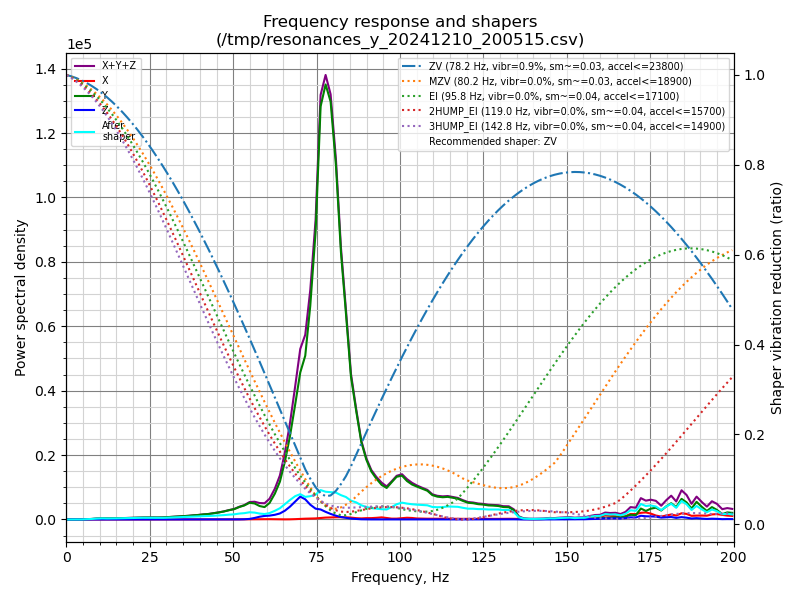
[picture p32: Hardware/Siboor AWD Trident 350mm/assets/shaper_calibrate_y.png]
Y-axis Shaper
| Gantry | Construction of the CNC Aluminum mounts and rails as well as the AWD motor system | Gantry   |
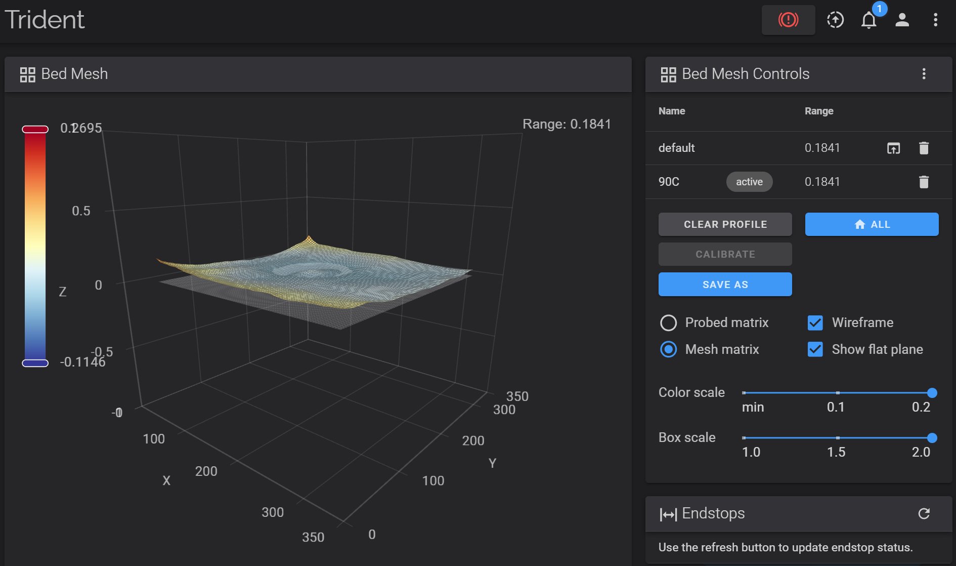
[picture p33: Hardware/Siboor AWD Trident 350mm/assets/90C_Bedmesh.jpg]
90C Bedmesh
| Bed | 1000W bed heater and magnetic pad on the 350mm Aluminum block | Bed Bed  |
| Electronics | Lots of stuff in here.  Started with HV/AC routing, and I wish I could have kept the HV lines in separate channel from LV wiring. Had to redrill/tap most of the holes in the bottom panel to allow the 48v/5v PSUs in addition to the stock 24v PSU, but the 350mm has extra room to "expand" the floor plan beyond the stock one, which is the SAME on both the 350mm and 300mm kit just to keep it simple for Siboor.  You can see where the test layout of the PSUs were to include the additional 5V and 48V 200W (details on the [MODs page](MODs.md) for those). | Electronics Electronics Electronics Electronics Electronics |
| Panels | Door panel construction was very confusing on the orientation for the right fit with the seals, but got it. [Annex-Eng Panel clips](https://github.com/Annex-Engineering/Annex-Engineering_User_Mods/tree/main/Printers/All_Printers/annex_dev-Panel_2020_Clips_and_Hinges) MOD was money and I LOVE the [Clicky-Clacky Fridge door](https://github.com/tanaes/whopping_Voron_mods/tree/main/clickyclacky_door) MOD included in this kit | Panels Panels |
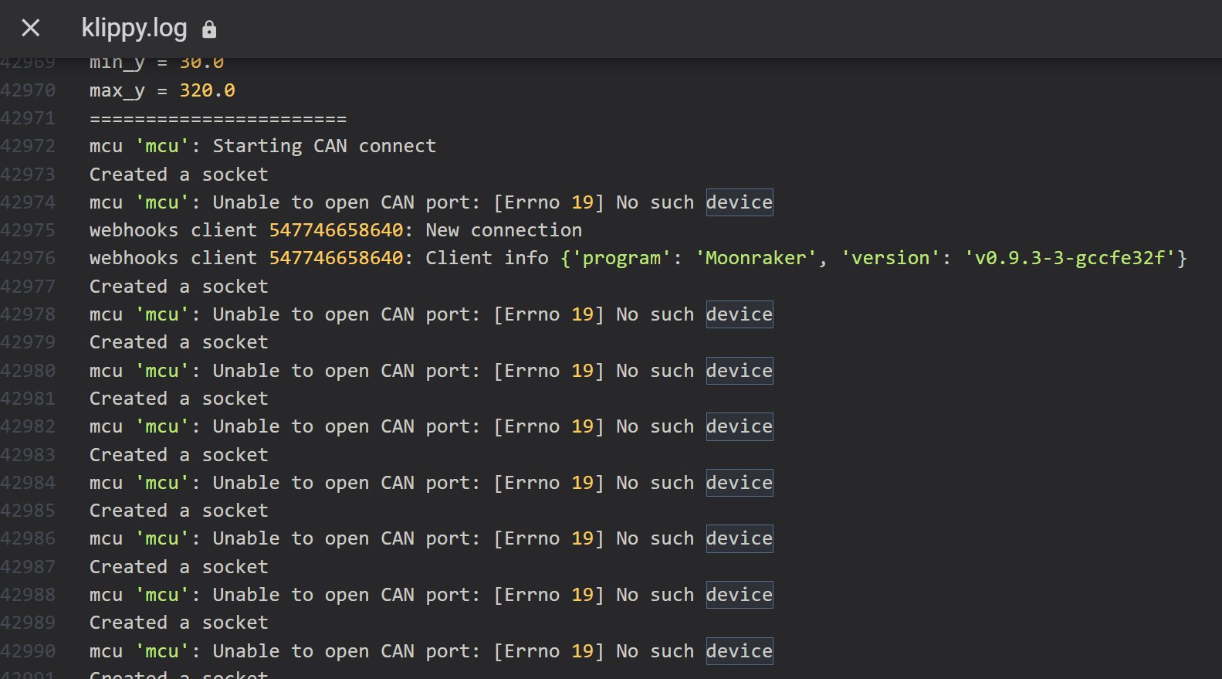
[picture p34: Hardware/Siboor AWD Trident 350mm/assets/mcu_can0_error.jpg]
Can0 bus error
| Misc | Firmware installation of canbus was VERY painful, but mostly because the Manta guide didn't really address it.  [Esoterical Canbus Guide](https://canbus.esoterical.online/) was a HUGE help here. |  UUID dump |

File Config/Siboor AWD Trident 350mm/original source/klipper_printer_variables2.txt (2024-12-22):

// printer['gcode'].commands = {'M110': {}, 'M112': {}, 'M115': {}, 'RESTART': {'help': 'Reload config file and restart host software'}, 'FIRMWARE_RESTART': {'help': 'Restart firmware, host, and reload config'}, 'ECHO': {}, 'STATUS': {'help': 'Report the printer status'}, 'HELP': {'help': 'Report the list of available extended G-Code commands'}, 'SAVE_CONFIG': {'help': 'Overwrite config file and restart'}, 'G1': {}, 'G20': {}, 'G21': {}, 'M82': {}, 'M83': {}, 'G90': {}, 'G91': {}, 'G92': {}, 'M220': {}, 'M221': {}, 'SET_GCODE_OFFSET': {'help': 'Set a virtual offset to g-code positions'}, 'SAVE_GCODE_STATE': {'help': 'Save G-Code coordinate state'}, 'RESTORE_GCODE_STATE': {'help': 'Restore a previously saved G-Code state'}, 'G0': {}, 'M114': {}, 'GET_POSITION': {'help': 'Return information on the current location of the toolhead'}, 'M20': {}, 'M21': {}, 'M23': {}, 'M26': {}, 'M27': {}, 'M28': {}, 'M29': {}, 'M30': {}, 'SDCARD_RESET_FILE': {'help': 'Clears a loaded SD File. Stops the print if necessary'}, 'SDCARD_PRINT_FILE': {'help': 'Loads a SD file and starts the print.  May include files in subdirectories.'}, 'G2': {}, 'G3': {}, 'G17': {}, 'G18': {}, 'G19': {}, 'EXCLUDE_OBJECT_START': {'help': 'Marks the beginning the current object as labeled'}, 'EXCLUDE_OBJECT_END': {'help': 'Marks the end the current object'}, 'EXCLUDE_OBJECT': {'help': 'Cancel moves inside a specified objects'}, 'EXCLUDE_OBJECT_DEFINE': {'help': 'Provides a summary of an object'}, 'M118': {}, 'RESPOND': {'help': 'Echo the message prepended with a prefix'}, 'M73': {}, 'M117': {}, 'SET_DISPLAY_TEXT': {'help': 'Set or clear the display message'}, 'STEPPER_BUZZ': {'help': 'Oscillate a given stepper to help id it'}, 'FORCE_MOVE': {'help': 'Manually move a stepper; invalidates kinematics'}, 'SET_KINEMATIC_POSITION': {'help': 'Force a low-level kinematic position'}, '_EXCITATE_AXIS_AT_FREQ': {'help': 'Maintain a specified excitation frequency for a period of time to diagnose and locate a source of vibrations'}, '_AXES_MAP_CALIBRATION': {'help': 'Perform a set of movements to measure the orientation of the accelerometer and help you set the best axes_map configuration for your printer'}, '_COMPARE_BELTS_RESPONSES': {'help': 'Perform a custom half-axis test to analyze and compare the frequency profiles of individual belts on CoreXY or CoreXZ printers'}, '_AXES_SHAPER_CALIBRATION': {'help': 'Perform standard axis input shaper tests on one or both XY axes to select the best input shaper filter'}, '_CREATE_VIBRATIONS_PROFILE': {'help': 'Run a series of motions to find speed/angle ranges where the printer could be exposed to VFAs to optimize your slicer speed profiles and TMC driver parameters'}, 'EXCITATE_AXIS_AT_FREQ': {'help': 'Maintain a specified excitation frequency for a period of time to diagnose and locate a source of vibrations'}, 'SET_GCODE_VARIABLE': {'help': 'Set the value of a G-Code macro variable'}, 'AXES_MAP_CALIBRATION': {'help': 'Perform a set of movements to measure the orientation of the accelerometer and help you set the best axes_map configuration for your printer'}, 'COMPARE_BELTS_RESPONSES': {'help': 'Perform a custom half-axis test to analyze and compare the frequency profiles of individual belts on CoreXY or CoreXZ printers'}, 'AXES_SHAPER_CALIBRATION': {'help': 'Perform standard axis input shaper tests on one or both XY axes to select the best input shaper filter'}, 'CREATE_VIBRATIONS_PROFILE': {'help': 'Run a series of motions to find speed/angle ranges where the printer could be exposed to VFAs to optimize your slicer speed profiles and TMC driver parameters'}, '_STATUS_VARIABLES': {'help': 'G-Code macro'}, 'SET_STATUS': {'help': 'Set Printer Status'}, 'RESET_STATUS': {'help': 'G-Code macro'}, '_EFFECT_STATUS': {'help': 'G-Code macro'}, '_STATUS_CONSOLE': {'help': 'G-Code macro'}, '_STATUS_KLIPPER_SCREEN': {'help': 'G-Code macro'}, 'CALIBRATE_HOTEND': {'help': 'Run PID calibration on hotend at optional temp set in menu'}, 'CALIBRATE_BEDHEATER': {'help': 'Run PID calibration on bed heater at optional temp set in menu'}, 'RUN_SHELL_COMMAND': {'help': 'Run a linux shell command'}, 'TEST_SPEED': {'help': 'Test for max speed and acceleration parameters for the printer. Procedure: Home -> ReadPositionFromMCU -> MovesToolhead@Vel&Accel -> Home -> ReadPositionfromMCU'}, 'DUMP_VARIABLES': {'help': "Macro to dump all printer variables excluding 'configfile'"}, 'UPDATE_DELAYED_GCODE': {'help': 'Update the duration of a delayed_gcode'}, 'START_PRINT': {'help': 'Common Start Print routine'}, 'PRINT_START': {'help': 'Common Start Print routine'}, 'END_PRINT': {'help': 'Common END Print routine'}, 'PRINT_END': {'help': 'G-Code macro'}, 'HOME_IF_NEEDED': {'help': 'G-Code macro'}, 'LOAD_FILAMENT': {'help': 'G-Code macro'}, 'UNLOAD_FILAMENT': {'help': 'G-Code macro'}, 'DROP_BED': {'help': 'Move bed down to lowest Level'}, 'DRAW_PRIMING_LINES': {'help': 'Purge lines at front of bed'}, 'HEAT_SOAK': {'help': 'Heats the bed and performs a soak.'}, 'CANCEL_HEAT_SOAK': {'help': 'Cancels an in-progress HEAT_SOAK cycle'}, '_SOAK_COMPLETE': {'help': 'Finish the soak command'}, 'RAZZLE_DAZZLE': {'help': 'Move head around the space fast! Fxxx is mm/min'}, 'M18': {}, 'M84': {}, 'SET_STEPPER_ENABLE': {'help': 'Enable/disable individual stepper by name'}, 'SET_TMC_FIELD': {'help': 'Set a register field of a TMC driver'}, 'INIT_TMC': {'help': 'Initialize TMC stepper driver registers'}, 'SET_TMC_CURRENT': {'help': 'Set the current of a TMC driver'}, 'DUMP_TMC': {'help': 'Read and display TMC stepper driver registers'}, 'M105': {}, 'TEMPERATURE_WAIT': {'help': 'Wait for a temperature on a sensor'}, 'QUERY_ADC': {'help': 'Report the last value of an analog pin'}, 'PID_CALIBRATE': {'help': 'Run PID calibration test'}, 'M140': {}, 'SET_IDLE_TIMEOUT': {'help': 'Set the idle timeout in seconds'}, 'BED_MESH_PROFILE': {'help': 'Bed Mesh Persistent Storage management'}, 'BED_MESH_OUTPUT': {'help': 'Retrieve interpolated grid of probed z-points'}, 'BED_MESH_MAP': {'help': 'Serialize mesh and output to terminal'}, 'BED_MESH_CLEAR': {'help': 'Clear the Mesh so no z-adjustment is made'}, 'BED_MESH_OFFSET': {'help': 'Add X/Y offsets to the mesh lookup'}, 'PROBECALIBRATE': {'help': 'G-Code macro'}, 'G32': {'help': 'G-Code macro'}, 'SET_FAN_SPEED': {'help': 'Sets the speed of a fan'}, 'SET_LED': {'help': 'Set the color of an LED'}, 'SET_LED_TEMPLATE': {'help': 'Assign a display_template to an LED'}, 'SET_RETRACTION': {'help': 'Set firmware retraction parameters'}, 'GET_RETRACTION': {'help': 'Report firmware retraction paramters'}, 'G10': {}, 'G11': {}, 'SET_INPUT_SHAPER': {'help': 'Set cartesian parameters for input shaper'}, 'CARTOGRAPHER_MODEL_SELECT': {'help': 'Load named scanner model'}, 'CARTOGRAPHER_MODEL_SAVE': {'help': 'Save current scanner model'}, 'CARTOGRAPHER_MODEL_REMOVE': {'help': 'Remove saved scanner model'}, 'CARTOGRAPHER_MODEL_LIST': {'help': 'Remove saved scanner model'}, 'CARTO_MODEL_SELECT': {'help': 'Load named scanner model'}, 'CARTO_MODEL_SAVE': {'help': 'Save current scanner model'}, 'CARTO_MODEL_REMOVE': {'help': 'Remove saved scanner model'}, 'CARTO_MODEL_LIST': {'help': 'Remove saved scanner model'}, 'CARTOGRAPHER_STREAM': {'help': 'Enable Scanner Streaming'}, 'CARTOGRAPHER_QUERY': {'help': 'Take a sample from the sensor'}, 'CARTOGRAPHER_CALIBRATE': {'help': 'Calibrate scanner response curve'}, 'CARTOGRAPHER_THRESHOLD_SCAN': {'help': 'Scan THRESHOLD in TOUCH mode'}, 'CARTOGRAPHER_ESTIMATE_BACKLASH': {'help': 'Estimate Z axis backlash'}, 'CARTO_STREAM': {'help': 'Enable Scanner Streaming'}, 'CARTO_QUERY': {'help': 'Take a sample from the sensor'}, 'CARTO_CALIBRATE': {'help': 'Calibrate scanner response curve'}, 'CARTO_THRESHOLD_SCAN': {'help': 'Scan THRESHOLD in TOUCH mode'}, 'CARTO_ESTIMATE_BACKLASH': {'help': 'Estimate Z axis backlash'}, 'CARTO_TOUCH': {'help': 'Home in TOUCH mode'}, 'PROBE': {'help': 'Probe Z-height at current XY position'}, 'PROBE_ACCURACY': {'help': 'Probe Z-height accuracy at current XY position'}, 'PROBE_SWITCH': {'help': 'swith between scan and touch'}, 'Z_OFFSET_APPLY_PROBE': {'help': "Adjust the probe's z_offset"}, 'ACCELEROMETER_MEASURE': {'help': 'Start/stop accelerometer'}, 'ACCELEROMETER_QUERY': {'help': 'Query accelerometer for the current values'}, 'ACCELEROMETER_DEBUG_READ': {'help': 'Query register (for debugging)'}, 'ACCELEROMETER_DEBUG_WRITE': {'help': 'Set register (for debugging)'}, 'MEASURE_AXES_NOISE': {'help': 'Measures noise of all enabled accelerometer chips'}, 'SHAPER_CALIBRATE': {'help': 'Simular to TEST_RESONANCES but suggest input shaper config'}, 'PROBE_CALIBRATE': {'help': 'G-Code macro'}, 'DATA_SAMPLE': {'help': 'G-Code macro'}, 'SYNC_MOTORS': {'help': 'Start motors synchronization'}, 'SYNC_MOTORS_CALIBRATE': {'help': 'Calibrate synchronization process model'}, 'SYNC_MOTORS_STATS': {'help': 'Show statistics'}, 'SET_TEMPERATURE_FAN_TARGET': {'help': 'Sets a temperature fan target and fan speed limits'}, 'M106': {'help': 'Set Fan [0,2,3] to speed 0-255'}, 'CLEAR_PAUSE': {'help': 'Clears the current paused state without resuming the print'}, 'SET_PAUSE_NEXT_LAYER': {'help': 'Enable a pause if the next layer is reached'}, 'SET_PAUSE_AT_LAYER': {'help': 'Enable/disable a pause if a given layer number is reached'}, '_TOOLHEAD_PARK_PAUSE_CANCEL': {'help': 'Helper: park toolhead used in PAUSE and CANCEL_PRINT'}, '_CLIENT_EXTRUDE': {'help': 'Extrudes, if the extruder is hot enough'}, '_CLIENT_RETRACT': {'help': 'Retracts, if the extruder is hot enough'}, '_CLIENT_LINEAR_MOVE': {'help': 'Linear move with save and restore of the gcode state'}, 'SET_ACTIVE_SPOOL': {'help': 'G-Code macro'}, 'CLEAR_ACTIVE_SPOOL': {'help': 'G-Code macro'}, 'GET_TIMELAPSE_SETUP': {'help': 'Print the Timelapse setup'}, '_SET_TIMELAPSE_SETUP': {'help': 'Set user parameters for timelapse'}, 'TIMELAPSE_TAKE_FRAME': {'help': 'Take Timelapse shoot'}, '_TIMELAPSE_NEW_FRAME': {'help': 'action call for timelapse shoot. must be a seperate macro'}, 'HYPERLAPSE': {'help': 'Start/Stop a hyperlapse recording'}, 'TIMELAPSE_RENDER': {'help': 'Render Timelapse video and wait for the result'}, 'TEST_STREAM_DELAY': {'help': 'Helper macro to find stream and park delay'}, 'QUERY_ENDSTOPS': {'help': 'Report on the status of each endstop'}, 'M119': {}, 'G4': {}, 'M400': {}, 'SET_VELOCITY_LIMIT': {'help': 'Set printer velocity limits'}, 'M204': {}, 'MANUAL_PROBE': {'help': 'Start manual probe helper script'}, 'TUNING_TOWER': {'help': 'Tool to adjust a parameter at each Z height'}, 'SET_PRESSURE_ADVANCE': {'help': 'Set pressure advance parameters'}, 'SET_EXTRUDER_ROTATION_DISTANCE': {'help': 'Set extruder rotation distance'}, 'SYNC_EXTRUDER_MOTION': {'help': 'Set extruder stepper motion queue'}, 'M104': {}, 'ACTIVATE_EXTRUDER': {'help': 'Change the active extruder'}, 'M24.1': {'help': "Renamed builtin of 'M24'"}, 'M24': {'help': 'Resume/Pause Print'}, 'M25.1': {'help': "Renamed builtin of 'M25'"}, 'M25': {'help': 'Pause Print'}, 'Z_TILT_ADJUST_SI': {'help': "Renamed builtin of 'Z_TILT_ADJUST'"}, 'Z_TILT_ADJUST': {'help': 'Level Bed to fixed gantry'}, 'TURN_OFF_HEATERS_SI': {'help': "Renamed builtin of 'TURN_OFF_HEATERS'"}, 'TURN_OFF_HEATERS': {'help': 'G-Code macro'}, 'SET_HEATER_TEMPERATURE_SI': {'help': "Renamed builtin of 'SET_HEATER_TEMPERATURE'"}, 'SET_HEATER_TEMPERATURE': {'help': 'G-Code macro'}, 'M109.1': {'help': "Renamed builtin of 'M109'"}, 'M109': {'help': 'G-Code macro'}, 'M190.1': {'help': "Renamed builtin of 'M190'"}, 'M190': {'help': 'G-Code macro'}, 'G28.1': {'help': "Renamed builtin of 'G28'"}, 'G28': {'help': 'G-Code macro'}, 'BED_MESH_CALIBRATE_SI': {'help': "Renamed builtin of 'BED_MESH_CALIBRATE'"}, 'BED_MESH_CALIBRATE': {'help': 'G-Code macro'}, 'TEST_RESONANCES_SI': {'help': "Renamed builtin of 'TEST_RESONANCES'"}, 'TEST_RESONANCES': {'help': 'G-Code macro'}, 'CARTOGRAPHER_TOUCH_SI': {'help': "Renamed builtin of 'CARTOGRAPHER_TOUCH'"}, 'CARTOGRAPHER_TOUCH': {'help': 'G-Code macro'}, 'PAUSE_BASE': {'help': "Renamed builtin of 'PAUSE'"}, 'PAUSE': {'help': 'Pause the actual running print'}, 'RESUME_BASE': {'help': "Renamed builtin of 'RESUME'"}, 'RESUME': {'help': 'Resume the actual running print'}, 'CANCEL_PRINT_BASE': {'help': "Renamed builtin of 'CANCEL_PRINT'"}, 'CANCEL_PRINT': {'help': 'Cancel the actual running print'}, 'SET_PRINT_STATS_INFO_BASE': {'help': "Renamed builtin of 'SET_PRINT_STATS_INFO'"}, 'SET_PRINT_STATS_INFO': {'help': 'Overwrite, to get pause_next_layer and pause_at_layer feature'}}
// printer['webhooks'].state = ready
// printer['webhooks'].state_message = Printer is ready
// printer['configfile'].warnings = []
// printer['configfile'].save_config_pending = False
// printer['configfile'].save_config_pending_items = {}
// printer['mcu'].mcu_version = v0.12.0-396-gb7233d119
// printer['mcu'].mcu_build_versions = gcc: (15:12.2.rel1-1) 12.2.1 20221205 binutils: (2.40-2+18+b1) 2.40
// printer['mcu'].mcu_constants = {'ADC_MAX': 4095, 'BUS_PINS_i2c1_PB6_PB7': 'PB6,PB7', 'BUS_PINS_i2c1_PB8_PB9': 'PB8,PB9', 'BUS_PINS_i2c2_PB10_PB11': 'PB10,PB11', 'BUS_PINS_i2c3_PA8_PC9': 'PA8,PC9', 'BUS_PINS_spi1': 'PA6,PA7,PA5', 'BUS_PINS_spi1a': 'PB4,PB5,PB3', 'BUS_PINS_spi2': 'PB14,PB15,PB13', 'BUS_PINS_spi2a': 'PC2,PC3,PB10', 'BUS_PINS_spi3a': 'PC11,PC12,PC10', 'BUS_PINS_spi4': 'PE13,PE14,PE12', 'BUS_PINS_spi5': 'PF8,PF9,PF7', 'BUS_PINS_spi5a': 'PH7,PF11,PH6', 'BUS_PINS_spi6': 'PG12,PG14,PG13', 'CANBUS_BRIDGE': 1, 'CLOCK_FREQ': 400000000, 'MCU': 'stm32h723xx', 'PWM_MAX': 255, 'RECEIVE_WINDOW': 192, 'RESERVE_PINS_CAN': 'PD0,PD1', 'RESERVE_PINS_USB': 'PA11,PA12', 'RESERVE_PINS_crystal': 'PH0,PH1', 'STATS_SUMSQ_BASE': 256, 'STEPPER_BOTH_EDGE': 1}
// printer['mcu'].last_stats = {'mcu_awake': 0.003, 'mcu_task_avg': 2e-06, 'mcu_task_stddev': 3e-06, 'bytes_write': 35535, 'bytes_read': 62496, 'bytes_retransmit': 0, 'bytes_invalid': 0, 'send_seq': 1764, 'receive_seq': 1764, 'retransmit_seq': 0, 'srtt': 0.001, 'rttvar': 0.0, 'rto': 0.025, 'ready_bytes': 0, 'upcoming_bytes': 0, 'freq': 399994604}
// printer['mcu THB'].mcu_version = v0.12.0-396-gb7233d119
// printer['mcu THB'].mcu_build_versions = gcc: (15:12.2.rel1-1) 12.2.1 20221205 binutils: (2.40-2+18+b1) 2.40
// printer['mcu THB'].mcu_constants = {'ADC_MAX': 4095, 'BUS_PINS_i2c1_PA9_PA10': 'PA9,PA10', 'BUS_PINS_i2c1_PB6_PB7': 'PB6,PB7', 'BUS_PINS_i2c1_PB8_PB9': 'PB8,PB9', 'BUS_PINS_i2c2_PB10_PB11': 'PB10,PB11', 'BUS_PINS_i2c2_PB13_PB14': 'PB13,PB14', 'BUS_PINS_i2c3_PB3_PB4': 'PB3,PB4', 'BUS_PINS_i2c3_PC0_PC1': 'PC0,PC1', 'BUS_PINS_spi1': 'PA6,PA7,PA5', 'BUS_PINS_spi1a': 'PB4,PB5,PB3', 'BUS_PINS_spi2': 'PB14,PB15,PB13', 'BUS_PINS_spi2_PB2_PB11_PB10': 'PB2,PB11,PB10', 'BUS_PINS_spi2a': 'PC2,PC3,PB10', 'BUS_PINS_spi3': 'PB4,PB5,PB3', 'CANBUS_FREQUENCY': 1000000, 'CLOCK_FREQ': 64000000, 'MCU': 'stm32g0b1xx', 'PWM_MAX': 255, 'RECEIVE_WINDOW': 192, 'RESERVE_PINS_CAN': 'PB0,PB1', 'RESERVE_PINS_crystal': 'PF0,PF1', 'STATS_SUMSQ_BASE': 256, 'STEPPER_BOTH_EDGE': 1}
// printer['mcu THB'].last_stats = {'mcu_awake': 0.002, 'mcu_task_avg': 1.5e-05, 'mcu_task_stddev': 2.1e-05, 'bytes_write': 4497, 'bytes_read': 24420, 'bytes_retransmit': 0, 'bytes_invalid': 0, 'send_seq': 468, 'receive_seq': 468, 'retransmit_seq': 0, 'srtt': 0.001, 'rttvar': 0.0, 'rto': 0.025, 'ready_bytes': 0, 'upcoming_bytes': 0, 'freq': 63999920, 'adj': 64000710}
// printer['gcode_move'].speed_factor = 1.0
// printer['gcode_move'].speed = 24000.0
// printer['gcode_move'].extrude_factor = 1.0
// printer['gcode_move'].absolute_coordinates = True
// printer['gcode_move'].absolute_extrude = True
// printer['gcode_move'].homing_origin = Coord(x=0.0, y=0.0, z=0.0, e=0.0)
// printer['gcode_move'].position = Coord(x=175.0, y=175.0, z=10.0, e=0.0)
// printer['gcode_move'].gcode_position = Coord(x=175.0, y=175.0, z=10.0, e=0.0)
// printer['print_stats'].filename =
// printer['print_stats'].total_duration = 0.0
// printer['print_stats'].print_duration = 0.0
// printer['print_stats'].filament_used = 0.0
// printer['print_stats'].state = standby
// printer['print_stats'].message =
// printer['print_stats'].info = {'total_layer': None, 'current_layer': None}
// printer['virtual_sdcard'].file_path = None
// printer['virtual_sdcard'].progress = 0.0
// printer['virtual_sdcard'].is_active = False
// printer['virtual_sdcard'].file_position = 0
// printer['virtual_sdcard'].file_size = 0
// printer['exclude_object'].objects = []
// printer['exclude_object'].excluded_objects = []
// printer['exclude_object'].current_object = None
// printer['display_status'].progress = 0.0
// printer['display_status'].message = Ready
// printer['gcode_macro excitate_axis_at_freq'] = {}
// printer['gcode_macro axes_map_calibration'] = {}
// printer['gcode_macro compare_belts_responses'] = {}
// printer['gcode_macro axes_shaper_calibration'] = {}
// printer['gcode_macro create_vibrations_profile'] = {}
// printer['gcode_macro _STATUS_VARIABLES'].printer_status = READY
// printer['gcode_macro _STATUS_VARIABLES'].status_effect_macros = ['_STATUS_CONSOLE', '_STATUS_KLIPPER_SCREEN']
// printer['gcode_macro SET_STATUS'] = {}
// printer['gcode_macro RESET_STATUS'] = {}
// printer['gcode_macro _EFFECT_STATUS'] = {}
// printer['gcode_macro _STATUS_CONSOLE'] = {}
// printer['gcode_macro _STATUS_KLIPPER_SCREEN'] = {}
// printer['gcode_macro M24'] = {}
// printer['gcode_macro M25'] = {}
// printer['gcode_macro Z_TILT_ADJUST'] = {}
// printer['gcode_macro TURN_OFF_HEATERS'] = {}
// printer['gcode_macro SET_HEATER_TEMPERATURE'] = {}
// printer['gcode_macro M109'] = {}
// printer['gcode_macro M190'] = {}
// printer['gcode_macro G28'] = {}
// printer['gcode_macro BED_MESH_CALIBRATE'] = {}
// printer['gcode_macro TEST_RESONANCES'] = {}
// printer['gcode_macro CARTOGRAPHER_TOUCH'] = {}
// printer['gcode_macro Calibrate_Hotend'] = {}
// printer['gcode_macro Calibrate_BedHeater'] = {}
// printer['gcode_macro TEST_SPEED'] = {}
// printer['gcode_macro DUMP_VARIABLES'] = {}
// printer['gcode_macro START_PRINT'] = {}
// printer['gcode_macro PRINT_START'].adaptive_mesh = 'false'
// printer['gcode_macro END_PRINT'] = {}
// printer['gcode_macro PRINT_END'] = {}
// printer['gcode_macro HOME_IF_NEEDED'] = {}
// printer['gcode_macro PAUSE'].extrude = 1.0
// printer['gcode_macro RESUME'].last_extruder_temp = {'restore': False, 'temp': 0}
// printer['gcode_macro RESUME'].restore_idle_timeout = 0
// printer['gcode_macro RESUME'].idle_state = False
// printer['gcode_macro CANCEL_PRINT'].park = True
// printer['gcode_macro LOAD_FILAMENT'].load_distance = 50
// printer['gcode_macro LOAD_FILAMENT'].purge_distance = 25
// printer['gcode_macro UNLOAD_FILAMENT'].unload_distance = 50
// printer['gcode_macro UNLOAD_FILAMENT'].purge_distance = 25
// printer['gcode_macro Drop_Bed'] = {}
// printer['gcode_macro DRAW_PRIMING_LINES'] = {}
// printer['gcode_macro HEAT_SOAK'].target_chamber_temp = 0
// printer['gcode_macro HEAT_SOAK'].target_bed_temp = 0
// printer['gcode_macro HEAT_SOAK'].stage = None
// printer['gcode_macro HEAT_SOAK'].check_interval = 10
// printer['gcode_macro HEAT_SOAK'].soak_time_remaining = 0
// printer['gcode_macro HEAT_SOAK'].total_time_elapsed = 0
// printer['gcode_macro CANCEL_HEAT_SOAK'] = {}
// printer['gcode_macro _SOAK_COMPLETE'] = {}
// printer['gcode_macro Razzle_Dazzle'] = {}
// printer['stepper_enable'].steppers = {'stepper_x': True, 'stepper_x1': True, 'stepper_y': True, 'stepper_y1': True, 'stepper_z': True, 'stepper_z1': True, 'stepper_z2': True, 'extruder': False}
// printer['tmc5160 stepper_x'].mcu_phase_offset = 75
// printer['tmc5160 stepper_x'].phase_offset_position = 350.54375
// printer['tmc5160 stepper_x'].run_current = 1.196925541070979
// printer['tmc5160 stepper_x'].hold_current = 1.196925541070979
// printer['tmc5160 stepper_x'].drv_status = {'sg_result': 58, 'cs_actual': 31, 'stallguard': 1, 'stst': 1}
// printer['tmc5160 stepper_x'].temperature = None
// printer['tmc5160 stepper_x1'].mcu_phase_offset = 117
// printer['tmc5160 stepper_x1'].phase_offset_position = 350.80625
// printer['tmc5160 stepper_x1'].run_current = 1.196925541070979
// printer['tmc5160 stepper_x1'].hold_current = 1.196925541070979
// printer['tmc5160 stepper_x1'].drv_status = {'sg_result': 50, 'cs_actual': 31, 'stallguard': 1, 'stst': 1}
// printer['tmc5160 stepper_x1'].temperature = None
// printer['tmc5160 stepper_y'].mcu_phase_offset = 55
// printer['tmc5160 stepper_y'].phase_offset_position = 0.40625
// printer['tmc5160 stepper_y'].run_current = 1.196925541070979
// printer['tmc5160 stepper_y'].hold_current = 1.196925541070979
// printer['tmc5160 stepper_y'].drv_status = {'sg_result': 51, 'cs_actual': 31, 'stallguard': 1, 'stst': 1}
// printer['tmc5160 stepper_y'].temperature = None
// printer['tmc5160 stepper_y1'].mcu_phase_offset = 97
// printer['tmc5160 stepper_y1'].phase_offset_position = 0.6687500000000001
// printer['tmc5160 stepper_y1'].run_current = 1.196925541070979
// printer['tmc5160 stepper_y1'].hold_current = 1.196925541070979
// printer['tmc5160 stepper_y1'].drv_status = {'sg_result': 48, 'cs_actual': 31, 'stallguard': 1, 'stst': 1}
// printer['tmc5160 stepper_y1'].temperature = None
// printer['tmc2209 stepper_z'].mcu_phase_offset = 9
// printer['tmc2209 stepper_z'].phase_offset_position = 9.859598245509119
// printer['tmc2209 stepper_z'].run_current = 0.7954951288348658
// printer['tmc2209 stepper_z'].hold_current = 0.7954951288348658
// printer['tmc2209 stepper_z'].drv_status = {'cs_actual': 25, 'stst': 1}
// printer['tmc2209 stepper_z'].temperature = None
// printer['tmc2209 stepper_z1'].mcu_phase_offset = 5
// printer['tmc2209 stepper_z1'].phase_offset_position = 9.854598245509118
// printer['tmc2209 stepper_z1'].run_current = 0.7954951288348658
// printer['tmc2209 stepper_z1'].hold_current = 0.7954951288348658
// printer['tmc2209 stepper_z1'].drv_status = {'cs_actual': 25, 'stst': 1}
// printer['tmc2209 stepper_z1'].temperature = None
// printer['tmc2209 stepper_z2'].mcu_phase_offset = 55
// printer['tmc2209 stepper_z2'].phase_offset_position = 9.917098245509118
// printer['tmc2209 stepper_z2'].run_current = 0.7954951288348658
// printer['tmc2209 stepper_z2'].hold_current = 0.7954951288348658
// printer['tmc2209 stepper_z2'].drv_status = {'cs_actual': 25, 'stst': 1}
// printer['tmc2209 stepper_z2'].temperature = None
// printer['heaters'].available_heaters = ['heater_bed', 'extruder']
// printer['heaters'].available_sensors = ['heater_bed', 'temperature_sensor MCU_THB', 'temperature_sensor cartographer_coil', 'temperature_sensor MCU_Carto', 'temperature_sensor MCU_Manta', 'temperature_sensor CM4', 'temperature_sensor Chamber_Top', 'temperature_sensor Chamber_Bottom', 'temperature_fan Electronics_Bay', 'extruder']
// printer['heaters'].available_monitors = []
// printer['heater_bed'].temperature = 24.15
// printer['heater_bed'].target = 0.0
// printer['heater_bed'].power = 0.0
// printer['idle_timeout'].state = Ready
// printer['idle_timeout'].printing_time = 0.0
// printer['bed_mesh'].profile_name =
// printer['bed_mesh'].mesh_min = (0.0, 0.0)
// printer['bed_mesh'].mesh_max = (0.0, 0.0)
// printer['bed_mesh'].probed_matrix = [[]]
// printer['bed_mesh'].mesh_matrix = [[]]
// printer['bed_mesh'].profiles = {'default': {'points': ((0.193619, 0.173019, 0.166346, 0.168486, 0.165894, 0.157469, 0.146174, 0.141552, 0.136189, 0.128524, 0.126803, 0.125379, 0.121295, 0.120886, 0.121336, 0.120347, 0.121925, 0.122573, 0.119572, 0.128776, 0.129234, 0.115154, 0.110883, 0.1111, 0.113932, 0.116815, 0.11678, 0.116168, 0.123541, 0.127911), (0.159436, 0.146569, 0.140021, 0.141942, 0.139623, 0.131614, 0.121603, 0.119213, 0.11419, 0.109947, 0.109586, 0.106997, 0.104292, 0.104028, 0.103007, 0.104731, 0.106314, 0.107734, 0.104275, 0.106512, 0.105535, 0.09847, 0.09638, 0.096324, 0.101842, 0.105081, 0.105155, 0.104357, 0.109802, 0.115422), (0.134608, 0.120454, 0.114979, 0.116927, 0.115784, 0.108256, 0.100487, 0.096555, 0.09535, 0.090712, 0.090835, 0.088864, 0.086649, 0.087884, 0.088041, 0.088911, 0.090619, 0.093021, 0.088971, 0.090231, 0.089121, 0.085761, 0.083925, 0.084214, 0.089446, 0.093468, 0.093995, 0.092159, 0.098367, 0.102524), (0.117183, 0.103906, 0.099063, 0.100469, 0.099164, 0.093748, 0.086677, 0.085094, 0.084064, 0.081242, 0.081831, 0.081554, 0.079183, 0.079896, 0.081225, 0.084078, 0.086941, 0.088028, 0.083851, 0.083521, 0.084204, 0.082597, 0.081175, 0.080186, 0.084285, 0.086114, 0.084869, 0.083888, 0.088924, 0.095656), (0.100662, 0.086582, 0.081401, 0.083382, 0.082766, 0.078576, 0.073816, 0.071849, 0.0702, 0.067299, 0.068244, 0.069732, 0.068516, 0.069828, 0.071633, 0.073405, 0.07541, 0.077915, 0.075325, 0.075214, 0.076764, 0.076403, 0.074503, 0.072636, 0.075724, 0.07721, 0.077758, 0.078901, 0.083904, 0.091841), (0.086732, 0.074903, 0.069415, 0.072291, 0.072218, 0.067918, 0.061938, 0.062601, 0.061787, 0.058126, 0.061191, 0.061602, 0.061461, 0.06317, 0.066509, 0.068596, 0.07042, 0.073199, 0.070987, 0.070731, 0.071692, 0.071919, 0.070782, 0.068971, 0.072236, 0.075017, 0.076351, 0.074661, 0.078783, 0.086779), (0.072067, 0.060009, 0.05504, 0.057888, 0.059931, 0.056593, 0.050918, 0.050629, 0.049907, 0.047737, 0.049928, 0.051383, 0.051227, 0.052933, 0.056979, 0.057872, 0.060105, 0.063173, 0.061826, 0.063271, 0.063594, 0.063709, 0.061763, 0.060751, 0.064439, 0.067345, 0.068171, 0.069358, 0.073928, 0.081062), (0.062313, 0.052208, 0.049108, 0.051497, 0.052125, 0.050238, 0.04559, 0.044769, 0.044757, 0.041152, 0.043874, 0.045737, 0.045635, 0.046121, 0.04994, 0.052781, 0.054906, 0.057233, 0.056664, 0.056512, 0.056384, 0.056488, 0.055559, 0.054989, 0.059144, 0.061816, 0.061997, 0.063213, 0.068242, 0.076492), (0.057084, 0.045133, 0.040571, 0.04378, 0.04403, 0.042282, 0.03833, 0.037043, 0.034102, 0.030646, 0.033383, 0.036041, 0.035421, 0.038307, 0.041077, 0.045356, 0.04739, 0.050039, 0.049073, 0.047946, 0.048971, 0.048197, 0.047341, 0.047446, 0.050841, 0.054645, 0.05596, 0.056802, 0.061887, 0.070199), (0.057518, 0.044058, 0.039616, 0.041912, 0.041242, 0.038678, 0.035517, 0.032738, 0.029595, 0.026027, 0.027549, 0.029892, 0.030237, 0.03292, 0.037618, 0.041053, 0.043969, 0.045879, 0.04319, 0.043593, 0.043618, 0.042953, 0.044364, 0.044698, 0.048142, 0.050837, 0.050298, 0.051549, 0.057375, 0.066196), (0.053478, 0.040048, 0.034081, 0.036715, 0.037394, 0.035263, 0.030563, 0.028202, 0.024421, 0.020425, 0.020695, 0.023576, 0.025546, 0.027253, 0.030193, 0.035252, 0.038116, 0.040898, 0.037924, 0.037644, 0.039353, 0.037921, 0.039989, 0.039973, 0.043888, 0.045299, 0.045562, 0.047473, 0.053359, 0.062482), (0.051712, 0.038027, 0.032755, 0.036482, 0.035129, 0.032735, 0.028056, 0.024848, 0.021554, 0.017387, 0.017635, 0.020679, 0.021898, 0.025539, 0.029186, 0.033243, 0.035501, 0.036954, 0.034669, 0.03487, 0.03518, 0.036226, 0.038077, 0.040476, 0.044944, 0.046479, 0.04594, 0.048513, 0.053669, 0.063735), (0.046092, 0.031478, 0.027687, 0.030096, 0.031062, 0.026708, 0.023198, 0.019429, 0.016045, 0.011698, 0.012678, 0.016169, 0.019372, 0.022675, 0.026262, 0.028624, 0.031558, 0.032022, 0.032589, 0.033039, 0.033632, 0.035322, 0.037457, 0.039913, 0.044494, 0.04594, 0.04742, 0.049073, 0.055085, 0.063729), (0.040195, 0.02432, 0.018882, 0.021512, 0.020432, 0.018197, 0.013547, 0.009508, 0.007284, 0.004528, 0.006416, 0.010032, 0.014225, 0.016847, 0.020568, 0.023939, 0.026634, 0.028621, 0.026603, 0.02803, 0.030808, 0.033489, 0.035592, 0.037549, 0.043128, 0.045203, 0.047277, 0.048092, 0.054129, 0.062432), (0.033206, 0.016325, 0.009088, 0.011948, 0.010672, 0.00668, 0.001297, -0.001976, -0.00293, -0.00553, -0.002564, 0.001714, 0.004719, 0.008581, 0.012976, 0.016367, 0.017905, 0.020302, 0.019006, 0.02233, 0.024633, 0.027577, 0.029864, 0.032794, 0.039965, 0.042678, 0.043862, 0.046328, 0.050808, 0.058261), (0.029042, 0.010151, 0.004027, 0.006204, 0.004163, -0.000992, -0.00686, -0.009368, -0.010707, -0.01213, -0.008404, -0.005446, -0.002012, 0.001756, 0.005676, 0.010369, 0.013333, 0.015538, 0.014602, 0.017759, 0.02068, 0.024048, 0.026956, 0.031197, 0.037644, 0.040957, 0.041992, 0.044523, 0.047713, 0.055794), (0.016225, 0.004985, -0.000746, -0.001022, -0.002435, -0.008347, -0.012504, -0.016856, -0.018286, -0.018815, -0.015271, -0.011061, -0.009116, -0.005895, -0.002381, 0.000761, 0.005876, 0.010422, 0.009209, 0.012241, 0.015853, 0.018799, 0.023332, 0.027648, 0.033877, 0.035746, 0.039025, 0.041857, 0.046773, 0.051219), (0.013015, 0.00339, -0.003239, -0.002622, -0.005507, -0.010618, -0.015715, -0.019135, -0.021366, -0.020959, -0.018093, -0.013152, -0.011034, -0.009963, -0.007652, -0.004024, 0.003075, 0.008575, 0.007197, 0.011702, 0.015314, 0.017515, 0.02143, 0.025789, 0.031982, 0.035649, 0.038086, 0.043856, 0.047922, 0.048579), (0.008817, 0.002404, -0.007528, -0.007964, -0.009541, -0.013317, -0.019526, -0.022222, -0.025394, -0.024295, -0.019562, -0.015847, -0.014104, -0.014677, -0.012405, -0.007672, -7.4e-05, 0.004512, 0.003631, 0.007974, 0.010999, 0.013247, 0.01801, 0.023422, 0.029823, 0.032338, 0.03563, 0.041566, 0.047607, 0.050906), (0.005703, 0.000109, -0.009172, -0.012016, -0.01285, -0.017875, -0.021289, -0.024669, -0.026258, -0.02624, -0.020395, -0.017392, -0.016598, -0.01494, -0.011578, -0.008012, -0.00055, 0.005281, 0.004121, 0.007118, 0.008765, 0.01167, 0.015782, 0.021444, 0.028205, 0.03047, 0.036311, 0.041843, 0.049652, 0.054852), (0.001317, -0.000726, -0.013004, -0.016836, -0.017278, -0.021085, -0.024626, -0.026482, -0.028063, -0.027668, -0.023376, -0.020908, -0.019606, -0.018187, -0.014308, -0.009236, -0.001633, 0.004278, 0.002249, 0.004071, 0.005229, 0.008792, 0.012999, 0.018735, 0.024609, 0.027572, 0.032413, 0.040271, 0.051181, 0.056963), (-0.002612, -0.005947, -0.018802, -0.021837, -0.022129, -0.023806, -0.028183, -0.028334, -0.029274, -0.029106, -0.02626, -0.023459, -0.021778, -0.019159, -0.014009, -0.008548, -0.002426, 0.002582, 0.001308, 0.003082, 0.004764, 0.008354, 0.012863, 0.017685, 0.024599, 0.026867, 0.030765, 0.041146, 0.052697, 0.061464), (-0.003229, -0.007845, -0.022006, -0.024396, -0.023536, -0.025903, -0.028515, -0.028766, -0.028714, -0.030233, -0.027509, -0.024308, -0.021524, -0.017417, -0.011733, -0.006582, 0.001137, 0.005762, 0.004243, 0.006554, 0.007538, 0.011022, 0.016436, 0.021624, 0.029589, 0.031799, 0.034584, 0.044331, 0.057757, 0.068142), (-0.001934, -0.011943, -0.024916, -0.0247, -0.022834, -0.023326, -0.026401, -0.02485, -0.026053, -0.027977, -0.023952, -0.022056, -0.017501, -0.012719, -0.004963, 0.002843, 0.008556, 0.014824, 0.014118, 0.014952, 0.016565, 0.018975, 0.023444, 0.027922, 0.035623, 0.037222, 0.039129, 0.049826, 0.062839, 0.072016), (-0.000812, -0.015587, -0.024693, -0.023447, -0.020346, -0.019697, -0.021991, -0.020873, -0.02167, -0.024015, -0.019982, -0.017692, -0.01223, -0.005088, 0.002038, 0.009726, 0.017462, 0.021694, 0.019964, 0.021223, 0.021456, 0.023695, 0.02743, 0.031884, 0.037176, 0.039038, 0.041649, 0.051111, 0.062486, 0.073351), (-0.002082, -0.015041, -0.021038, -0.018135, -0.014811, -0.013542, -0.015322, -0.012543, -0.011655, -0.013919, -0.011708, -0.007746, -0.002884, 0.004431, 0.012205, 0.020427, 0.028368, 0.0323, 0.029324, 0.029378, 0.028179, 0.031056, 0.033054, 0.036632, 0.042581, 0.04325, 0.045372, 0.053733, 0.064421, 0.073504), (-0.001045, -0.01341, -0.015712, -0.010636, -0.006441, -0.007358, -0.00691, -0.003058, -0.001425, -0.004704, -0.001249, 0.003099, 0.007985, 0.014644, 0.020736, 0.029415, 0.036968, 0.039532, 0.036755, 0.036568, 0.036098, 0.037576, 0.039334, 0.041893, 0.047222, 0.046594, 0.048038, 0.055489, 0.066565, 0.075133), (0.007269, -0.003569, -0.007321, -0.000515, 0.002351, 0.003812, 0.004344, 0.008968, 0.010141, 0.007848, 0.012498, 0.015633, 0.021426, 0.028041, 0.0347, 0.042616, 0.049119, 0.051081, 0.04844, 0.04886, 0.047293, 0.048279, 0.049865, 0.050477, 0.053217, 0.053936, 0.054588, 0.063135, 0.073278, 0.080805), (0.019353, 0.00807, 0.00569, 0.010956, 0.013771, 0.016215, 0.01743, 0.02254, 0.022276, 0.020041, 0.023667, 0.029585, 0.035688, 0.040934, 0.047361, 0.054658, 0.06118, 0.063438, 0.059345, 0.05842, 0.056897, 0.060999, 0.068906, 0.067073, 0.067914, 0.062252, 0.062088, 0.070688, 0.081789, 0.090747), (0.035356, 0.022483, 0.018032, 0.023252, 0.028047, 0.029735, 0.031815, 0.03694, 0.036751, 0.03523, 0.038171, 0.043824, 0.049127, 0.05681, 0.064048, 0.068958, 0.074736, 0.076815, 0.071358, 0.070816, 0.070685, 0.085492, 0.085477, 0.084358, 0.08525, 0.077605, 0.074589, 0.082538, 0.09249, 0.10127)), 'mesh_params': OrderedDict([('min_x', 30.0), ('max_x', 320.0), ('min_y', 30.0), ('max_y', 320.0), ('x_count', 30), ('y_count', 30), ('mesh_x_pps', 2), ('mesh_y_pps', 2), ('algo', 'bicubic'), ('tension', 0.2)])}, '100C': {'points': ((0.21187, 0.190201, 0.185444, 0.186434, 0.184566, 0.175918, 0.166453, 0.16197, 0.156232, 0.149864, 0.148622, 0.147684, 0.144017, 0.143795, 0.144288, 0.144726, 0.145876, 0.145539, 0.143662, 0.153313, 0.15329, 0.136743, 0.132283, 0.131218, 0.134924, 0.137066, 0.13676, 0.135219, 0.140978, 0.144791), (0.174473, 0.161727, 0.157073, 0.159387, 0.156234, 0.14947, 0.140748, 0.138188, 0.135299, 0.130247, 0.129735, 0.128593, 0.125126, 0.125496, 0.126251, 0.12701, 0.128871, 0.130405, 0.126694, 0.130138, 0.127181, 0.11953, 0.115981, 0.116464, 0.121225, 0.123668, 0.123309, 0.121547, 0.126657, 0.131952), (0.147811, 0.132884, 0.128184, 0.13112, 0.129321, 0.122504, 0.116609, 0.113998, 0.113449, 0.109878, 0.111784, 0.110666, 0.109546, 0.109655, 0.110474, 0.11141, 0.113475, 0.115837, 0.111052, 0.1111, 0.111197, 0.106359, 0.103318, 0.10345, 0.108697, 0.111035, 0.111069, 0.109579, 0.112784, 0.118401), (0.126094, 0.111706, 0.106922, 0.109488, 0.108063, 0.104155, 0.097046, 0.096673, 0.097069, 0.09469, 0.095754, 0.096184, 0.096306, 0.096716, 0.097825, 0.100999, 0.103763, 0.105184, 0.100871, 0.100568, 0.10103, 0.098266, 0.096118, 0.094205, 0.098205, 0.099597, 0.098524, 0.096836, 0.100933, 0.107206), (0.106832, 0.093087, 0.087078, 0.089936, 0.090836, 0.087344, 0.081979, 0.081261, 0.08102, 0.079457, 0.082521, 0.083191, 0.083567, 0.085609, 0.088758, 0.091299, 0.093796, 0.094912, 0.092824, 0.092871, 0.093361, 0.09185, 0.089581, 0.085794, 0.088846, 0.09035, 0.090086, 0.089354, 0.093608, 0.101054), (0.090696, 0.077479, 0.072672, 0.077225, 0.078115, 0.074228, 0.069157, 0.069318, 0.069318, 0.068409, 0.071169, 0.072717, 0.072495, 0.074823, 0.077992, 0.082169, 0.085038, 0.086609, 0.084626, 0.084165, 0.084751, 0.084026, 0.081297, 0.07958, 0.082366, 0.085233, 0.084567, 0.083686, 0.087, 0.095588), (0.074965, 0.06263, 0.059195, 0.062703, 0.064681, 0.061586, 0.057356, 0.057274, 0.057125, 0.056266, 0.059147, 0.061853, 0.062303, 0.064652, 0.067883, 0.07128, 0.074744, 0.076267, 0.074857, 0.076051, 0.076958, 0.076501, 0.073491, 0.071148, 0.075305, 0.075603, 0.076675, 0.075803, 0.080168, 0.087551), (0.06297, 0.052979, 0.049225, 0.053828, 0.055919, 0.053166, 0.048538, 0.047999, 0.048098, 0.04675, 0.050025, 0.052551, 0.052609, 0.055011, 0.058728, 0.062247, 0.064831, 0.067376, 0.065681, 0.066067, 0.066143, 0.066207, 0.063892, 0.062159, 0.066002, 0.067879, 0.068555, 0.068434, 0.072734, 0.082391), (0.056647, 0.045003, 0.04132, 0.044978, 0.046461, 0.044772, 0.041289, 0.039866, 0.037358, 0.034928, 0.039078, 0.042031, 0.042757, 0.045231, 0.048521, 0.053163, 0.055512, 0.057564, 0.056917, 0.05635, 0.056058, 0.055888, 0.054556, 0.05349, 0.056961, 0.059941, 0.060214, 0.060333, 0.065163, 0.074552), (0.054681, 0.043045, 0.038942, 0.041482, 0.042577, 0.040356, 0.036911, 0.03511, 0.032623, 0.028822, 0.031996, 0.034006, 0.035753, 0.039156, 0.043801, 0.047429, 0.049616, 0.051763, 0.050262, 0.050318, 0.049658, 0.04883, 0.049075, 0.048989, 0.053272, 0.053881, 0.053847, 0.053606, 0.060151, 0.067999), (0.053085, 0.038579, 0.033512, 0.036979, 0.037485, 0.03681, 0.032542, 0.029995, 0.027445, 0.023592, 0.024187, 0.027806, 0.030068, 0.03252, 0.037013, 0.040775, 0.043581, 0.045887, 0.042924, 0.044525, 0.044453, 0.043641, 0.044238, 0.045174, 0.049549, 0.050151, 0.048944, 0.050517, 0.055539, 0.065338), (0.047753, 0.035577, 0.030842, 0.033834, 0.034539, 0.032539, 0.027748, 0.024999, 0.022677, 0.018189, 0.019086, 0.022778, 0.024955, 0.027846, 0.031649, 0.036045, 0.039464, 0.041043, 0.039326, 0.039692, 0.039459, 0.039577, 0.041388, 0.042979, 0.0477, 0.048553, 0.04838, 0.049146, 0.05463, 0.064969), (0.042616, 0.028386, 0.023868, 0.027749, 0.027799, 0.025786, 0.022363, 0.018604, 0.01503, 0.011366, 0.014651, 0.017633, 0.020981, 0.023997, 0.027527, 0.030515, 0.034505, 0.035998, 0.035249, 0.036207, 0.036905, 0.039116, 0.040588, 0.042127, 0.046188, 0.047377, 0.048309, 0.049681, 0.055161, 0.063772), (0.035432, 0.01949, 0.014946, 0.018457, 0.018818, 0.014827, 0.010695, 0.007768, 0.005835, 0.003832, 0.005804, 0.009596, 0.013764, 0.018039, 0.019999, 0.024486, 0.026942, 0.02969, 0.028237, 0.029682, 0.031934, 0.033892, 0.036429, 0.038628, 0.044333, 0.045407, 0.046774, 0.047829, 0.052885, 0.062453), (0.029867, 0.011551, 0.004822, 0.008472, 0.007308, 0.003794, -0.001244, -0.003365, -0.00484, -0.005432, -0.002896, 0.001216, 0.003963, 0.008534, 0.012389, 0.016675, 0.019851, 0.020772, 0.020354, 0.022985, 0.025093, 0.02792, 0.030696, 0.033726, 0.039974, 0.042614, 0.043833, 0.045747, 0.050016, 0.058121), (0.02194, 0.003787, -0.000526, 0.00313, -0.000346, -0.004895, -0.009482, -0.012226, -0.01216, -0.012566, -0.008886, -0.004933, -0.001391, 0.001497, 0.005549, 0.010151, 0.012599, 0.015153, 0.015139, 0.018683, 0.021105, 0.024605, 0.02789, 0.033252, 0.038202, 0.040054, 0.042052, 0.044153, 0.047908, 0.055593), (0.010224, -0.001342, -0.006299, -0.006373, -0.007515, -0.01274, -0.01675, -0.020476, -0.021454, -0.020462, -0.016978, -0.012521, -0.008474, -0.00643, -0.003336, 0.000915, 0.006014, 0.010193, 0.009362, 0.012265, 0.014882, 0.019035, 0.022471, 0.027153, 0.032595, 0.034505, 0.038138, 0.041012, 0.045542, 0.049676), (0.005674, -0.004486, -0.009876, -0.00923, -0.011938, -0.016002, -0.019988, -0.023642, -0.025525, -0.024377, -0.019483, -0.015681, -0.012089, -0.009455, -0.008773, -0.005139, 0.001626, 0.006908, 0.005073, 0.009229, 0.011854, 0.016209, 0.020092, 0.024787, 0.031322, 0.034368, 0.036299, 0.040119, 0.045294, 0.046427), (0.001289, -0.004906, -0.014285, -0.01357, -0.014679, -0.018428, -0.023231, -0.026315, -0.029008, -0.027937, -0.022064, -0.016537, -0.014696, -0.014834, -0.011773, -0.007452, -0.000649, 0.003858, 0.003388, 0.00719, 0.010708, 0.012122, 0.016632, 0.022357, 0.029479, 0.031791, 0.035127, 0.040061, 0.046735, 0.048475), (-0.001699, -0.00694, -0.0162, -0.017437, -0.01828, -0.022479, -0.026867, -0.028671, -0.030782, -0.029427, -0.023141, -0.019074, -0.017388, -0.016702, -0.014372, -0.007634, -0.001931, 0.004344, 0.003813, 0.006381, 0.007837, 0.01006, 0.014754, 0.019351, 0.027142, 0.029875, 0.033869, 0.04102, 0.047999, 0.052664), (-0.006937, -0.009379, -0.021414, -0.023076, -0.023797, -0.027113, -0.030497, -0.031076, -0.032747, -0.032061, -0.027271, -0.023061, -0.021565, -0.019706, -0.015578, -0.009868, -0.002929, 0.002234, 0.00176, 0.003026, 0.004074, 0.007025, 0.011174, 0.016192, 0.024144, 0.026524, 0.030179, 0.038217, 0.047833, 0.05434), (-0.011184, -0.013664, -0.026612, -0.027857, -0.02881, -0.030141, -0.033713, -0.034407, -0.034199, -0.034169, -0.030357, -0.027165, -0.023426, -0.020425, -0.016405, -0.011523, -0.004507, -0.000131, -0.000673, 0.002083, 0.002806, 0.006541, 0.010887, 0.016432, 0.023149, 0.025914, 0.028578, 0.038525, 0.049635, 0.058583), (-0.012212, -0.017868, -0.030468, -0.032451, -0.030594, -0.032491, -0.034926, -0.033352, -0.034016, -0.034103, -0.030616, -0.028563, -0.024786, -0.020326, -0.013715, -0.00732, -0.000902, 0.00397, 0.003552, 0.006386, 0.007244, 0.010433, 0.014048, 0.020838, 0.02752, 0.028563, 0.032098, 0.041328, 0.054874, 0.064707), (-0.011294, -0.020381, -0.032368, -0.031852, -0.028799, -0.029333, -0.032242, -0.030437, -0.031133, -0.032732, -0.028619, -0.02492, -0.020652, -0.014359, -0.008303, 0.000223, 0.008054, 0.012034, 0.011157, 0.013303, 0.01399, 0.017233, 0.021134, 0.025757, 0.03147, 0.033533, 0.03666, 0.046206, 0.057868, 0.066947), (-0.009275, -0.023907, -0.033065, -0.030615, -0.025595, -0.02584, -0.028107, -0.025713, -0.026764, -0.028854, -0.024169, -0.020911, -0.015228, -0.008388, 0.001048, 0.008567, 0.01651, 0.021644, 0.019797, 0.019907, 0.019938, 0.022538, 0.025914, 0.030825, 0.035601, 0.036003, 0.039549, 0.049499, 0.059484, 0.068921), (-0.010172, -0.02306, -0.029832, -0.024663, -0.02052, -0.019347, -0.02043, -0.01715, -0.01705, -0.018207, -0.015155, -0.010307, -0.004578, 0.00309, 0.012831, 0.019409, 0.026751, 0.030761, 0.029278, 0.028569, 0.028478, 0.029484, 0.031, 0.035628, 0.040225, 0.041167, 0.042359, 0.051652, 0.061098, 0.069085), (-0.008267, -0.01911, -0.021972, -0.016291, -0.011278, -0.010332, -0.010382, -0.005888, -0.00375, -0.0058, -0.002449, -0.00034, 0.00742, 0.014523, 0.020916, 0.030996, 0.038499, 0.041055, 0.038312, 0.038262, 0.036099, 0.037129, 0.038901, 0.042353, 0.04627, 0.044882, 0.046345, 0.05412, 0.064524, 0.072449), (0.001889, -0.008425, -0.01091, -0.004321, -5e-05, 0.002541, 0.00424, 0.008915, 0.010681, 0.008512, 0.011996, 0.01696, 0.023066, 0.030175, 0.037086, 0.044946, 0.051629, 0.055661, 0.051615, 0.051433, 0.050146, 0.050887, 0.051147, 0.052425, 0.055681, 0.055199, 0.055198, 0.062594, 0.07215, 0.079362), (0.015047, 0.005694, 0.00216, 0.008453, 0.012819, 0.016386, 0.01747, 0.023842, 0.024888, 0.022134, 0.0262, 0.033432, 0.038941, 0.044825, 0.051637, 0.058602, 0.066107, 0.068473, 0.064464, 0.062874, 0.061749, 0.064828, 0.072141, 0.070953, 0.069669, 0.063396, 0.064095, 0.071661, 0.081227, 0.089011), (0.032902, 0.019991, 0.015324, 0.020459, 0.026796, 0.029734, 0.030858, 0.03725, 0.038192, 0.036669, 0.040944, 0.047439, 0.054841, 0.060812, 0.067843, 0.073157, 0.07956, 0.080861, 0.076053, 0.074822, 0.075312, 0.088591, 0.088978, 0.087683, 0.08712, 0.079279, 0.075851, 0.08188, 0.091943, 0.100624)), 'mesh_params': OrderedDict([('min_x', 30.0), ('max_x', 320.0), ('min_y', 30.0), ('max_y', 320.0), ('x_count', 30), ('y_count', 30), ('mesh_x_pps', 2), ('mesh_y_pps', 2), ('algo', 'bicubic'), ('tension', 0.2)])}}
// printer['z_tilt'].applied = False
// printer['gcode_macro PROBECALIBRATE'] = {}
// printer['gcode_macro G32'] = {}
// printer['tmc2209 extruder'].mcu_phase_offset = 3
// printer['tmc2209 extruder'].phase_offset_position = 0.00492875
// printer['tmc2209 extruder'].run_current = 0.6119193298729737
// printer['tmc2209 extruder'].hold_current = 0.6119193298729737
// printer['tmc2209 extruder'].drv_status = None
// printer['tmc2209 extruder'].temperature = None
// printer['fan_generic Part_Fan'].speed = 0.0
// printer['fan_generic Part_Fan'].rpm = None
// printer['heater_fan Hotend_Fan'].speed = 0.0
// printer['heater_fan Hotend_Fan'].rpm = None
// printer['temperature_sensor MCU_THB'].temperature = 33.23
// printer['temperature_sensor MCU_THB'].measured_min_temp = 33.07
// printer['temperature_sensor MCU_THB'].measured_max_temp = 33.67
// printer['neopixel th_led'].color_data = [(0.8, 0.8, 0.8, 0.0), (0.8, 0.8, 0.8, 0.0), (0.8, 0.8, 0.8, 0.0)]
// printer['firmware_retraction'].retract_length = 0.2
// printer['firmware_retraction'].retract_speed = 30.0
// printer['firmware_retraction'].unretract_extra_length = 0.0
// printer['firmware_retraction'].unretract_speed = 25.0
// printer['mcu scanner'].mcu_version = CARTOGRAPHER 5.1.0
// printer['mcu scanner'].mcu_build_versions =
// printer['mcu scanner'].mcu_constants = {'ADC_MAX': 4095, 'BUS_PINS_i2c1': 'PB6,PB7', 'BUS_PINS_spi1': 'PA6,PA7,PA5', 'CANBUS_FREQUENCY': 1000000, 'CARTOGRAPHER_ADC_SMOOTH_COUNT': 16, 'CLOCK_FREQ': 48000000, 'MCU': 'stm32f042x6', 'PWM_MAX': 2, 'RECEIVE_WINDOW': 192, 'RESERVE_PINS_CAN': 'PA11,PA12', 'RESERVE_PINS_crystal': 'PF0,PF1', 'STATS_SUMSQ_BASE': 256, 'STEPPER_BOTH_EDGE': 1}
// printer['mcu scanner'].last_stats = {'mcu_awake': 0.028, 'mcu_task_avg': 1.1e-05, 'mcu_task_stddev': 2.5e-05, 'bytes_write': 3239, 'bytes_read': 25144, 'bytes_retransmit': 0, 'bytes_invalid': 0, 'send_seq': 371, 'receive_seq': 371, 'retransmit_seq': 0, 'srtt': 0.001, 'rttvar': 0.0, 'rto': 0.025, 'ready_bytes': 0, 'upcoming_bytes': 0, 'freq': 47998229, 'adj': 47998809}
// printer['probe'].name = scanner
// printer['probe'].last_z_result = 0.0
// printer['temperature_sensor cartographer_coil'].temperature = 26.33
// printer['temperature_sensor cartographer_coil'].measured_min_temp = 26.08
// printer['temperature_sensor cartographer_coil'].measured_max_temp = 26.78
// printer['scanner'].last_sample = None
// printer['scanner'].last_received_sample = {'clock': 6682534484, 'data': 33498339, 'temp': 26.32902946611148, '#name': 'cartographer_data', '#sent_time': 19872.420504340003, '#receive_time': 19872.530526005998, 'time': 139.2083766249842, 'data_smooth': 33498317.608453423, 'freq': 2994982.9824376185, 'pos': [175.0, 175.0, 10.0], 'vel': 0.0}
// printer['scanner'].model = default
// printer['temperature_sensor MCU_Carto'].temperature = 39.67
// printer['temperature_sensor MCU_Carto'].measured_min_temp = 38.65
// printer['temperature_sensor MCU_Carto'].measured_max_temp = 40.78
// printer['gcode_macro PROBE_CALIBRATE'] = {}
// printer['gcode_macro DATA_SAMPLE'] = {}
// printer['motors_sync'].applied = False
// printer['temperature_sensor MCU_Manta'].temperature = 44.24
// printer['temperature_sensor MCU_Manta'].measured_min_temp = 42.45
// printer['temperature_sensor MCU_Manta'].measured_max_temp = 44.39
// printer['temperature_host CM4'].temperature = 48.2
// printer['temperature_sensor CM4'].temperature = 48.2
// printer['temperature_sensor CM4'].measured_min_temp = 45.76
// printer['temperature_sensor CM4'].measured_max_temp = 49.17
// printer['temperature_sensor Chamber_Top'].temperature = 25.85
// printer['temperature_sensor Chamber_Top'].measured_min_temp = 25.37
// printer['temperature_sensor Chamber_Top'].measured_max_temp = 25.88
// printer['temperature_sensor Chamber_Bottom'].temperature = 22.39
// printer['temperature_sensor Chamber_Bottom'].measured_min_temp = 22.28
// printer['temperature_sensor Chamber_Bottom'].measured_max_temp = 22.59
// printer['temperature_fan Electronics_Bay'].speed = 0.0
// printer['temperature_fan Electronics_Bay'].rpm = None
// printer['temperature_fan Electronics_Bay'].temperature = 32.63
// printer['temperature_fan Electronics_Bay'].target = 35.0
// printer['controller_fan Driver_Fan'].speed = 1.0
// printer['controller_fan Driver_Fan'].rpm = None
// printer['fan_generic Bed_Fan'].speed = 0.0
// printer['fan_generic Bed_Fan'].rpm = None
// printer['fan_generic Fume_Fan'].speed = 0.0
// printer['fan_generic Fume_Fan'].rpm = None
// printer['gcode_macro M106'] = {}
// printer['neopixel chamber'].color_data = [(0.8, 0.9, 0.4, 0.0), (0.8, 0.9, 0.4, 0.0), (0.8, 0.9, 0.4, 0.0), (0.8, 0.9, 0.4, 0.0), (0.8, 0.9, 0.4, 0.0), (0.8, 0.9, 0.4, 0.0), (0.8, 0.9, 0.4, 0.0), (0.8, 0.9, 0.4, 0.0), (0.8, 0.9, 0.4, 0.0), (0.8, 0.9, 0.4, 0.0), (0.8, 0.9, 0.4, 0.0), (0.8, 0.9, 0.4, 0.0), (0.8, 0.9, 0.4, 0.0), (0.8, 0.9, 0.4, 0.0), (0.8, 0.9, 0.4, 0.0), (0.8, 0.9, 0.4, 0.0), (0.8, 0.9, 0.4, 0.0), (0.8, 0.9, 0.4, 0.0), (0.8, 0.9, 0.4, 0.0), (0.8, 0.9, 0.4, 0.0), (0.8, 0.9, 0.4, 0.0), (0.8, 0.9, 0.4, 0.0), (0.8, 0.9, 0.4, 0.0), (0.8, 0.9, 0.4, 0.0), (0.8, 0.9, 0.4, 0.0), (0.8, 0.9, 0.4, 0.0), (0.8, 0.9, 0.4, 0.0), (0.8, 0.9, 0.4, 0.0), (0.8, 0.9, 0.4, 0.0), (0.8, 0.9, 0.4, 0.0), (0.8, 0.9, 0.4, 0.0), (0.8, 0.9, 0.4, 0.0), (0.8, 0.9, 0.4, 0.0), (0.8, 0.9, 0.4, 0.0), (0.8, 0.9, 0.4, 0.0), (0.8, 0.9, 0.4, 0.0), (0.8, 0.9, 0.4, 0.0), (0.8, 0.9, 0.4, 0.0), (0.8, 0.9, 0.4, 0.0), (0.8, 0.9, 0.4, 0.0), (0.8, 0.9, 0.4, 0.0), (0.8, 0.9, 0.4, 0.0), (0.8, 0.9, 0.4, 0.0), (0.8, 0.9, 0.4, 0.0), (0.8, 0.9, 0.4, 0.0), (0.8, 0.9, 0.4, 0.0), (0.8, 0.9, 0.4, 0.0), (0.8, 0.9, 0.4, 0.0), (0.8, 0.9, 0.4, 0.0), (0.8, 0.9, 0.4, 0.0), (0.8, 0.9, 0.4, 0.0), (0.8, 0.9, 0.4, 0.0), (0.8, 0.9, 0.4, 0.0), (0.8, 0.9, 0.4, 0.0), (0.8, 0.9, 0.4, 0.0), (0.8, 0.9, 0.4, 0.0), (0.8, 0.9, 0.4, 0.0), (0.8, 0.9, 0.4, 0.0), (0.8, 0.9, 0.4, 0.0), (0.8, 0.9, 0.4, 0.0), (0.8, 0.9, 0.4, 0.0), (0.8, 0.9, 0.4, 0.0), (0.8, 0.9, 0.4, 0.0), (0.8, 0.9, 0.4, 0.0), (0.8, 0.9, 0.4, 0.0), (0.8, 0.9, 0.4, 0.0), (0.8, 0.9, 0.4, 0.0), (0.8, 0.9, 0.4, 0.0), (0.8, 0.9, 0.4, 0.0), (0.8, 0.9, 0.4, 0.0), (0.8, 0.9, 0.4, 0.0), (0.8, 0.9, 0.4, 0.0)]
// printer['pause_resume'].is_paused = False
// printer['gcode_macro SET_PAUSE_NEXT_LAYER'] = {}
// printer['gcode_macro SET_PAUSE_AT_LAYER'] = {}
// printer['gcode_macro SET_PRINT_STATS_INFO'].pause_next_layer = {'enable': False, 'call': 'PAUSE'}
// printer['gcode_macro SET_PRINT_STATS_INFO'].pause_at_layer = {'enable': False, 'layer': 0, 'call': 'PAUSE'}
// printer['gcode_macro _TOOLHEAD_PARK_PAUSE_CANCEL'] = {}
// printer['gcode_macro _CLIENT_EXTRUDE'] = {}
// printer['gcode_macro _CLIENT_RETRACT'] = {}
// printer['gcode_macro _CLIENT_LINEAR_MOVE'] = {}
// printer['gcode_macro SET_ACTIVE_SPOOL'] = {}
// printer['gcode_macro CLEAR_ACTIVE_SPOOL'] = {}
// printer['gcode_macro GET_TIMELAPSE_SETUP'] = {}
// printer['gcode_macro _SET_TIMELAPSE_SETUP'] = {}
// printer['gcode_macro TIMELAPSE_TAKE_FRAME'].enable = True
// printer['gcode_macro TIMELAPSE_TAKE_FRAME'].takingframe = False
// printer['gcode_macro TIMELAPSE_TAKE_FRAME'].park = {'enable': False, 'pos': 'back_left', 'time': 0.1, 'custom': {'x': 10.0, 'y': 10.0, 'dz': 0.0}, 'coord': {'x': 0.0, 'y': 360.0, 'dz': 0}}
// printer['gcode_macro TIMELAPSE_TAKE_FRAME'].extruder = {'fw_retract': False, 'retract': 1.0, 'extrude': 1.0}
// printer['gcode_macro TIMELAPSE_TAKE_FRAME'].speed = {'travel': 100.0, 'retract': 15.0, 'extrude': 15.0}
// printer['gcode_macro TIMELAPSE_TAKE_FRAME'].verbose = False
// printer['gcode_macro TIMELAPSE_TAKE_FRAME'].check_time = 0.5
// printer['gcode_macro TIMELAPSE_TAKE_FRAME'].restore = {'absolute': {'coordinates': True, 'extrude': True}, 'speed': 1500, 'e': 0, 'factor': {'speed': 1.0, 'extrude': 1.0}}
// printer['gcode_macro TIMELAPSE_TAKE_FRAME'].macro = {'pause': 'PAUSE_BASE', 'resume': 'RESUME_BASE'}
// printer['gcode_macro TIMELAPSE_TAKE_FRAME'].is_paused = False
// printer['gcode_macro _TIMELAPSE_NEW_FRAME'] = {}
// printer['gcode_macro HYPERLAPSE'].cycle = 0
// printer['gcode_macro HYPERLAPSE'].run = False
// printer['gcode_macro TIMELAPSE_RENDER'].render = False
// printer['gcode_macro TIMELAPSE_RENDER'].run_identifier = 0
// printer['gcode_macro TEST_STREAM_DELAY'] = {}
// printer['motion_report'].live_position = Coord(x=175.0, y=175.0, z=10.0, e=0.0)
// printer['motion_report'].live_velocity = 0.0
// printer['motion_report'].live_extruder_velocity = 0.0
// printer['motion_report'].steppers = ['extruder', 'stepper_x', 'stepper_x1', 'stepper_y', 'stepper_y1', 'stepper_z', 'stepper_z1', 'stepper_z2']
// printer['motion_report'].trapq = ['extruder', 'toolhead']
// printer['query_endstops'].last_query = {}
// printer['system_stats'].sysload = 0.59375
// printer['system_stats'].cputime = 640.24231074
// printer['system_stats'].memavail = 3232264
// printer['manual_probe'].is_active = False
// printer['manual_probe'].z_position = None
// printer['manual_probe'].z_position_lower = None
// printer['manual_probe'].z_position_upper = None
// printer['toolhead'].homed_axes = xyz
// printer['toolhead'].axis_minimum = Coord(x=0.0, y=0.0, z=-5.0, e=0.0)
// printer['toolhead'].axis_maximum = Coord(x=350.0, y=360.0, z=245.0, e=0.0)
// printer['toolhead'].print_time = 123.22444863863274
// printer['toolhead'].stalls = 0
// printer['toolhead'].estimated_print_time = 139.3629716425
// printer['toolhead'].extruder = extruder
// printer['toolhead'].position = Coord(x=175.0, y=175.0, z=10.0, e=0.0)
// printer['toolhead'].max_velocity = 1000.0
// printer['toolhead'].max_accel = 5000.0
// printer['toolhead'].minimum_cruise_ratio = 0.5
// printer['toolhead'].square_corner_velocity = 5.0
// printer['extruder'].temperature = 27.43
// printer['extruder'].target = 0.0
// printer['extruder'].power = 0.0
// printer['extruder'].can_extrude = False
// printer['extruder'].pressure_advance = 0.04
// printer['extruder'].smooth_time = 0.04
// printer['extruder'].motion_queue = None

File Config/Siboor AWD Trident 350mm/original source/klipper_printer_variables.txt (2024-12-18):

printer['gcode'].commands = {'M110': {}, 'M112': {}, 'M115': {}, 'RESTART': {'help': 'Reload config file and restart host software'}, 'FIRMWARE_RESTART': {'help': 'Restart firmware, host, and reload config'}, 'ECHO': {}, 'STATUS': {'help': 'Report the printer status'}, 'HELP': {'help': 'Report the list of available extended G-Code commands'}, 'SAVE_CONFIG': {'help': 'Overwrite config file and restart'}, 'G1': {}, 'G20': {}, 'G21': {}, 'M82': {}, 'M83': {}, 'G90': {}, 'G91': {}, 'G92': {}, 'M220': {}, 'M221': {}, 'SET_GCODE_OFFSET': {'help': 'Set a virtual offset to g-code positions'}, 'SAVE_GCODE_STATE': {'help': 'Save G-Code coordinate state'}, 'RESTORE_GCODE_STATE': {'help': 'Restore a previously saved G-Code state'}, 'G0': {}, 'M114': {}, 'GET_POSITION': {'help': 'Return information on the current location of the toolhead'}, 'M20': {}, 'M21': {}, 'M23': {}, 'M26': {}, 'M27': {}, 'M28': {}, 'M29': {}, 'M30': {}, 'SDCARD_RESET_FILE': {'help': 'Clears a loaded SD File. Stops the print if necessary'}, 'SDCARD_PRINT_FILE': {'help': 'Loads a SD file and starts the print.  May include files in subdirectories.'}, 'G2': {}, 'G3': {}, 'G17': {}, 'G18': {}, 'G19': {}, 'EXCLUDE_OBJECT_START': {'help': 'Marks the beginning the current object as labeled'}, 'EXCLUDE_OBJECT_END': {'help': 'Marks the end the current object'}, 'EXCLUDE_OBJECT': {'help': 'Cancel moves inside a specified objects'}, 'EXCLUDE_OBJECT_DEFINE': {'help': 'Provides a summary of an object'}, 'M118': {}, 'RESPOND': {'help': 'Echo the message prepended with a prefix'}, 'M73': {}, 'M117': {}, 'SET_DISPLAY_TEXT': {'help': 'Set or clear the display message'}, 'STEPPER_BUZZ': {'help': 'Oscillate a given stepper to help id it'}, 'FORCE_MOVE': {'help': 'Manually move a stepper; invalidates kinematics'}, 'SET_KINEMATIC_POSITION': {'help': 'Force a low-level kinematic position'}, '_EXCITATE_AXIS_AT_FREQ': {'help': 'Maintain a specified excitation frequency for a period of time to diagnose and locate a source of vibrations'}, '_AXES_MAP_CALIBRATION': {'help': 'Perform a set of movements to measure the orientation of the accelerometer and help you set the best axes_map configuration for your printer'}, '_COMPARE_BELTS_RESPONSES': {'help': 'Perform a custom half-axis test to analyze and compare the frequency profiles of individual belts on CoreXY or CoreXZ printers'}, '_AXES_SHAPER_CALIBRATION': {'help': 'Perform standard axis input shaper tests on one or both XY axes to select the best input shaper filter'}, '_CREATE_VIBRATIONS_PROFILE': {'help': 'Run a series of motions to find speed/angle ranges where the printer could be exposed to VFAs to optimize your slicer speed profiles and TMC driver parameters'}, 'EXCITATE_AXIS_AT_FREQ': {'help': 'Maintain a specified excitation frequency for a period of time to diagnose and locate a source of vibrations'}, 'SET_GCODE_VARIABLE': {'help': 'Set the value of a G-Code macro variable'}, 'AXES_MAP_CALIBRATION': {'help': 'Perform a set of movements to measure the orientation of the accelerometer and help you set the best axes_map configuration for your printer'}, 'COMPARE_BELTS_RESPONSES': {'help': 'Perform a custom half-axis test to analyze and compare the frequency profiles of individual belts on CoreXY or CoreXZ printers'}, 'AXES_SHAPER_CALIBRATION': {'help': 'Perform standard axis input shaper tests on one or both XY axes to select the best input shaper filter'}, 'CREATE_VIBRATIONS_PROFILE': {'help': 'Run a series of motions to find speed/angle ranges where the printer could be exposed to VFAs to optimize your slicer speed profiles and TMC driver parameters'}, '_STATUS_VARIABLES': {'help': 'G-Code macro'}, 'SET_STATUS': {'help': 'Set Printer Status'}, 'RESET_STATUS': {'help': 'G-Code macro'}, '_EFFECT_STATUS': {'help': 'G-Code macro'}, '_STATUS_CONSOLE': {'help': 'G-Code macro'}, '_STATUS_KLIPPER_SCREEN': {'help': 'G-Code macro'}, 'CALIBRATE_HOTEND': {'help': 'Run PID calibration on hotend at optional temp set in menu'}, 'CALIBRATE_BEDHEATER': {'help': 'Run PID calibration on bed heater at optional temp set in menu'}, 'RUN_SHELL_COMMAND': {'help': 'Run a linux shell command'}, 'TEST_SPEED': {'help': 'Test for max speed and acceleration parameters for the printer. Procedure: Home -> ReadPositionFromMCU -> MovesToolhead@Vel&Accel -> Home -> ReadPositionfromMCU'}, 'DUMP_VARIABLES': {'help': "Macro to dump all printer variables excluding 'configfile'"}, 'UPDATE_DELAYED_GCODE': {'help': 'Update the duration of a delayed_gcode'}, '_START_PRINT': {'help': 'Common Start Print routine'}, 'PRINT_START': {'help': 'Common Start Print routine'}, '_END_PRINT': {'help': 'Common END Print routine'}, 'PRINT_END': {'help': 'G-Code macro'}, 'HOME_IF_NEEDED': {'help': 'G-Code macro'}, 'LOAD_FILAMENT': {'help': 'G-Code macro'}, 'UNLOAD_FILAMENT': {'help': 'G-Code macro'}, 'DRAW_PRIMING_LINES': {'help': 'Purge lines at front of bed'}, 'HEAT_SOAK': {'help': 'Heats the bed and performs a soak.'}, 'CANCEL_HEAT_SOAK': {'help': 'Cancels an in-progress HEAT_SOAK cycle'}, '_SOAK_COMPLETE': {'help': 'Finish the soak command'}, 'RAZZLE_DAZZLE': {'help': 'Move head around the space fast! Fxxx is mm/min'}, 'LED_STOP': {'help': 'G-Code macro'}, 'M18': {}, 'M84': {}, 'SET_STEPPER_ENABLE': {'help': 'Enable/disable individual stepper by name'}, 'SET_TMC_FIELD': {'help': 'Set a register field of a TMC driver'}, 'INIT_TMC': {'help': 'Initialize TMC stepper driver registers'}, 'SET_TMC_CURRENT': {'help': 'Set the current of a TMC driver'}, 'DUMP_TMC': {'help': 'Read and display TMC stepper driver registers'}, 'M105': {}, 'TEMPERATURE_WAIT': {'help': 'Wait for a temperature on a sensor'}, 'QUERY_ADC': {'help': 'Report the last value of an analog pin'}, 'PID_CALIBRATE': {'help': 'Run PID calibration test'}, 'M140': {}, 'SET_IDLE_TIMEOUT': {'help': 'Set the idle timeout in seconds'}, 'BED_MESH_PROFILE': {'help': 'Bed Mesh Persistent Storage management'}, 'BED_MESH_OUTPUT': {'help': 'Retrieve interpolated grid of probed z-points'}, 'BED_MESH_MAP': {'help': 'Serialize mesh and output to terminal'}, 'BED_MESH_CLEAR': {'help': 'Clear the Mesh so no z-adjustment is made'}, 'BED_MESH_OFFSET': {'help': 'Add X/Y offsets to the mesh lookup'}, 'PROBECALIBRATE': {'help': 'G-Code macro'}, 'G32': {'help': 'G-Code macro'}, 'SET_FAN_SPEED': {'help': 'Sets the speed of a fan'}, 'SET_LED': {'help': 'Set the color of an LED'}, 'SET_LED_TEMPLATE': {'help': 'Assign a display_template to an LED'}, 'SET_INPUT_SHAPER': {'help': 'Set cartesian parameters for input shaper'}, 'CARTOGRAPHER_MODEL_SELECT': {'help': 'Load named scanner model'}, 'CARTOGRAPHER_MODEL_SAVE': {'help': 'Save current scanner model'}, 'CARTOGRAPHER_MODEL_REMOVE': {'help': 'Remove saved scanner model'}, 'CARTOGRAPHER_MODEL_LIST': {'help': 'Remove saved scanner model'}, 'CARTO_MODEL_SELECT': {'help': 'Load named scanner model'}, 'CARTO_MODEL_SAVE': {'help': 'Save current scanner model'}, 'CARTO_MODEL_REMOVE': {'help': 'Remove saved scanner model'}, 'CARTO_MODEL_LIST': {'help': 'Remove saved scanner model'}, 'CARTOGRAPHER_STREAM': {'help': 'Enable Scanner Streaming'}, 'CARTOGRAPHER_QUERY': {'help': 'Take a sample from the sensor'}, 'CARTOGRAPHER_CALIBRATE': {'help': 'Calibrate scanner response curve'}, 'CARTOGRAPHER_THRESHOLD_SCAN': {'help': 'Scan THRESHOLD in TOUCH mode'}, 'CARTOGRAPHER_ESTIMATE_BACKLASH': {'help': 'Estimate Z axis backlash'}, 'CARTOGRAPHER_TOUCH': {'help': 'Home in TOUCH mode'}, 'CARTO_STREAM': {'help': 'Enable Scanner Streaming'}, 'CARTO_QUERY': {'help': 'Take a sample from the sensor'}, 'CARTO_CALIBRATE': {'help': 'Calibrate scanner response curve'}, 'CARTO_THRESHOLD_SCAN': {'help': 'Scan THRESHOLD in TOUCH mode'}, 'CARTO_ESTIMATE_BACKLASH': {'help': 'Estimate Z axis backlash'}, 'CARTO_TOUCH': {'help': 'Home in TOUCH mode'}, 'PROBE': {'help': 'Probe Z-height at current XY position'}, 'PROBE_ACCURACY': {'help': 'Probe Z-height accuracy at current XY position'}, 'PROBE_SWITCH': {'help': 'swith between scan and touch'}, 'Z_OFFSET_APPLY_PROBE': {'help': "Adjust the probe's z_offset"}, 'ACCELEROMETER_MEASURE': {'help': 'Start/stop accelerometer'}, 'ACCELEROMETER_QUERY': {'help': 'Query accelerometer for the current values'}, 'ACCELEROMETER_DEBUG_READ': {'help': 'Query register (for debugging)'}, 'ACCELEROMETER_DEBUG_WRITE': {'help': 'Set register (for debugging)'}, 'MEASURE_AXES_NOISE': {'help': 'Measures noise of all enabled accelerometer chips'}, 'TEST_RESONANCES': {'help': 'Runs the resonance test for a specifed axis'}, 'SHAPER_CALIBRATE': {'help': 'Simular to TEST_RESONANCES but suggest input shaper config'}, 'PROBE_CALIBRATE': {'help': 'G-Code macro'}, 'DATA_SAMPLE': {'help': 'G-Code macro'}, 'SYNC_MOTORS': {'help': 'Start motors synchronization'}, 'SYNC_MOTORS_CALIBRATE': {'help': 'Calibrate synchronization process'}, 'SYNC_MOTORS_STATS': {'help': 'Show statistics'}, 'SET_TEMPERATURE_FAN_TARGET': {'help': 'Sets a temperature fan target and fan speed limits'}, 'M106': {'help': 'Set Fan [0,2,3] to speed 0-255'}, 'STOP_LED_EFFECTS': {'help': 'Stops all led_effects'}, 'SET_LED_EFFECT': {'help': 'Starts or Stops the specified led_effect'}, '_LED_STATUS_OFF_TH': {'help': 'G-Code macro'}, '_STATUS_TH_LED': {'help': 'G-Code macro'}, '_LED_STATUS_IDLE_TH': {'help': 'G-Code macro'}, '_LED_STATUS_READY_TH': {'help': 'G-Code macro'}, '_LED_STATUS_PRINTING_TH': {'help': 'G-Code macro'}, 'LED_OFF': {'help': 'G-Code macro'}, 'LED_ON': {'help': 'G-Code macro'}, '_STATUS_CHAMBER_LED': {'help': 'G-Code macro'}, '_LED_STATUS_IDLE': {'help': 'G-Code macro'}, '_LED_STATUS_READY': {'help': 'G-Code macro'}, '_LED_STATUS_PRINTING': {'help': 'G-Code macro'}, '_LED_RAINBOW': {'help': 'G-Code macro'}, '_LED_RAINBOWGREG': {'help': 'G-Code macro'}, '_LED_EPILEPSIE': {'help': 'G-Code macro'}, '_LED_COMMET': {'help': 'G-Code macro'}, '_LED_DOUBLECOMMET': {'help': 'G-Code macro'}, 'LED_KITT': {'help': 'G-Code macro'}, '_LED_PACMAN': {'help': 'G-Code macro'}, '_LED_WHITE': {'help': 'G-Code macro'}, 'CLEAR_PAUSE': {'help': 'Clears the current paused state without resuming the print'}, 'SET_PAUSE_NEXT_LAYER': {'help': 'Enable a pause if the next layer is reached'}, 'SET_PAUSE_AT_LAYER': {'help': 'Enable/disable a pause if a given layer number is reached'}, '_TOOLHEAD_PARK_PAUSE_CANCEL': {'help': 'Helper: park toolhead used in PAUSE and CANCEL_PRINT'}, '_CLIENT_EXTRUDE': {'help': 'Extrudes, if the extruder is hot enough'}, '_CLIENT_RETRACT': {'help': 'Retracts, if the extruder is hot enough'}, '_CLIENT_LINEAR_MOVE': {'help': 'Linear move with save and restore of the gcode state'}, 'SET_ACTIVE_SPOOL': {'help': 'G-Code macro'}, 'CLEAR_ACTIVE_SPOOL': {'help': 'G-Code macro'}, 'GET_TIMELAPSE_SETUP': {'help': 'Print the Timelapse setup'}, '_SET_TIMELAPSE_SETUP': {'help': 'Set user parameters for timelapse'}, 'TIMELAPSE_TAKE_FRAME': {'help': 'Take Timelapse shoot'}, '_TIMELAPSE_NEW_FRAME': {'help': 'action call for timelapse shoot. must be a seperate macro'}, 'HYPERLAPSE': {'help': 'Start/Stop a hyperlapse recording'}, 'TIMELAPSE_RENDER': {'help': 'Render Timelapse video and wait for the result'}, 'TEST_STREAM_DELAY': {'help': 'Helper macro to find stream and park delay'}, 'QUERY_ENDSTOPS': {'help': 'Report on the status of each endstop'}, 'M119': {}, 'G4': {}, 'M400': {}, 'SET_VELOCITY_LIMIT': {'help': 'Set printer velocity limits'}, 'M204': {}, 'MANUAL_PROBE': {'help': 'Start manual probe helper script'}, 'TUNING_TOWER': {'help': 'Tool to adjust a parameter at each Z height'}, 'SET_PRESSURE_ADVANCE': {'help': 'Set pressure advance parameters'}, 'SET_EXTRUDER_ROTATION_DISTANCE': {'help': 'Set extruder rotation distance'}, 'SYNC_EXTRUDER_MOTION': {'help': 'Set extruder stepper motion queue'}, 'M104': {}, 'M109': {}, 'ACTIVATE_EXTRUDER': {'help': 'Change the active extruder'}, 'M24.1': {'help': "Renamed builtin of 'M24'"}, 'M24': {'help': 'Resume/Pause Print'}, 'M25.1': {'help': "Renamed builtin of 'M25'"}, 'M25': {'help': 'Pause Print'}, 'Z_TILT_ADJUST_SI': {'help': "Renamed builtin of 'Z_TILT_ADJUST'"}, 'Z_TILT_ADJUST': {'help': 'Level Bed to fixed gantry'}, 'TURN_OFF_HEATERS_SI': {'help': "Renamed builtin of 'TURN_OFF_HEATERS'"}, 'TURN_OFF_HEATERS': {'help': 'G-Code macro'}, 'SET_HEATER_TEMPERATURE_SI': {'help': "Renamed builtin of 'SET_HEATER_TEMPERATURE'"}, 'SET_HEATER_TEMPERATURE': {'help': 'G-Code macro'}, 'M190.1': {'help': "Renamed builtin of 'M190'"}, 'M190': {'help': 'G-Code macro'}, 'G28.1': {'help': "Renamed builtin of 'G28'"}, 'G28': {'help': 'G-Code macro'}, 'BED_MESH_CALIBRATE_SI': {'help': "Renamed builtin of 'BED_MESH_CALIBRATE'"}, 'BED_MESH_CALIBRATE': {'help': 'G-Code macro'}, 'PAUSE_BASE': {'help': "Renamed builtin of 'PAUSE'"}, 'PAUSE': {'help': 'Pause the actual running print'}, 'RESUME_BASE': {'help': "Renamed builtin of 'RESUME'"}, 'RESUME': {'help': 'Resume the actual running print'}, 'CANCEL_PRINT_BASE': {'help': "Renamed builtin of 'CANCEL_PRINT'"}, 'CANCEL_PRINT': {'help': 'Cancel the actual running print'}, 'SET_PRINT_STATS_INFO_BASE': {'help': "Renamed builtin of 'SET_PRINT_STATS_INFO'"}, 'SET_PRINT_STATS_INFO': {'help': 'Overwrite, to get pause_next_layer and pause_at_layer feature'}}
printer['webhooks'].state = ready
printer['webhooks'].state_message = Printer is ready
printer['configfile'].warnings = []
printer['configfile'].save_config_pending = False
printer['configfile'].save_config_pending_items = {}
printer['mcu'].mcu_version = v0.12.0-396-gb7233d119
printer['mcu'].mcu_build_versions = gcc: (15:12.2.rel1-1) 12.2.1 20221205 binutils: (2.40-2+18+b1) 2.40
printer['mcu'].mcu_constants = {'ADC_MAX': 4095, 'BUS_PINS_i2c1_PB6_PB7': 'PB6,PB7', 'BUS_PINS_i2c1_PB8_PB9': 'PB8,PB9', 'BUS_PINS_i2c2_PB10_PB11': 'PB10,PB11', 'BUS_PINS_i2c3_PA8_PC9': 'PA8,PC9', 'BUS_PINS_spi1': 'PA6,PA7,PA5', 'BUS_PINS_spi1a': 'PB4,PB5,PB3', 'BUS_PINS_spi2': 'PB14,PB15,PB13', 'BUS_PINS_spi2a': 'PC2,PC3,PB10', 'BUS_PINS_spi3a': 'PC11,PC12,PC10', 'BUS_PINS_spi4': 'PE13,PE14,PE12', 'BUS_PINS_spi5': 'PF8,PF9,PF7', 'BUS_PINS_spi5a': 'PH7,PF11,PH6', 'BUS_PINS_spi6': 'PG12,PG14,PG13', 'CANBUS_BRIDGE': 1, 'CLOCK_FREQ': 400000000, 'MCU': 'stm32h723xx', 'PWM_MAX': 255, 'RECEIVE_WINDOW': 192, 'RESERVE_PINS_CAN': 'PD0,PD1', 'RESERVE_PINS_USB': 'PA11,PA12', 'RESERVE_PINS_crystal': 'PH0,PH1', 'STATS_SUMSQ_BASE': 256, 'STEPPER_BOTH_EDGE': 1}
printer['mcu'].last_stats = {'mcu_awake': 0.001, 'mcu_task_avg': 1e-06, 'mcu_task_stddev': 1e-06, 'bytes_write': 5110, 'bytes_read': 11246, 'bytes_retransmit': 0, 'bytes_invalid': 0, 'send_seq': 339, 'receive_seq': 339, 'retransmit_seq': 0, 'srtt': 0.0, 'rttvar': 0.0, 'rto': 0.025, 'ready_bytes': 0, 'upcoming_bytes': 0, 'freq': 399994436}
printer['mcu THB'].mcu_version = v0.12.0-396-gb7233d119
printer['mcu THB'].mcu_build_versions = gcc: (15:12.2.rel1-1) 12.2.1 20221205 binutils: (2.40-2+18+b1) 2.40
printer['mcu THB'].mcu_constants = {'ADC_MAX': 4095, 'BUS_PINS_i2c1_PA9_PA10': 'PA9,PA10', 'BUS_PINS_i2c1_PB6_PB7': 'PB6,PB7', 'BUS_PINS_i2c1_PB8_PB9': 'PB8,PB9', 'BUS_PINS_i2c2_PB10_PB11': 'PB10,PB11', 'BUS_PINS_i2c2_PB13_PB14': 'PB13,PB14', 'BUS_PINS_i2c3_PB3_PB4': 'PB3,PB4', 'BUS_PINS_i2c3_PC0_PC1': 'PC0,PC1', 'BUS_PINS_spi1': 'PA6,PA7,PA5', 'BUS_PINS_spi1a': 'PB4,PB5,PB3', 'BUS_PINS_spi2': 'PB14,PB15,PB13', 'BUS_PINS_spi2_PB2_PB11_PB10': 'PB2,PB11,PB10', 'BUS_PINS_spi2a': 'PC2,PC3,PB10', 'BUS_PINS_spi3': 'PB4,PB5,PB3', 'CANBUS_FREQUENCY': 1000000, 'CLOCK_FREQ': 64000000, 'MCU': 'stm32g0b1xx', 'PWM_MAX': 255, 'RECEIVE_WINDOW': 192, 'RESERVE_PINS_CAN': 'PB0,PB1', 'RESERVE_PINS_crystal': 'PF0,PF1', 'STATS_SUMSQ_BASE': 256, 'STEPPER_BOTH_EDGE': 1}
printer['mcu THB'].last_stats = {'mcu_awake': 0.003, 'mcu_task_avg': 1.5e-05, 'mcu_task_stddev': 2.1e-05, 'bytes_write': 1563, 'bytes_read': 6638, 'bytes_retransmit': 0, 'bytes_invalid': 0, 'send_seq': 165, 'receive_seq': 165, 'retransmit_seq': 0, 'srtt': 0.001, 'rttvar': 0.0, 'rto': 0.025, 'ready_bytes': 0, 'upcoming_bytes': 0, 'freq': 63999948, 'adj': 63999529}
printer['gcode_move'].speed_factor = 1.0
printer['gcode_move'].speed = 1500.0
printer['gcode_move'].extrude_factor = 1.0
printer['gcode_move'].absolute_coordinates = True
printer['gcode_move'].absolute_extrude = True
printer['gcode_move'].homing_origin = Coord(x=0.0, y=0.0, z=0.0, e=0.0)
printer['gcode_move'].position = Coord(x=0.0, y=0.0, z=0.0, e=0.0)
printer['gcode_move'].gcode_position = Coord(x=0.0, y=0.0, z=0.0, e=0.0)
printer['print_stats'].filename = 
printer['print_stats'].total_duration = 0.0
printer['print_stats'].print_duration = 0.0
printer['print_stats'].filament_used = 0.0
printer['print_stats'].state = standby
printer['print_stats'].message = 
printer['print_stats'].info = {'total_layer': None, 'current_layer': None}
printer['virtual_sdcard'].file_path = None
printer['virtual_sdcard'].progress = 0.0
printer['virtual_sdcard'].is_active = False
printer['virtual_sdcard'].file_position = 0
printer['virtual_sdcard'].file_size = 0
printer['exclude_object'].objects = []
printer['exclude_object'].excluded_objects = []
printer['exclude_object'].current_object = None
printer['display_status'].progress = 0.0
printer['display_status'].message = Ready
printer['gcode_macro excitate_axis_at_freq'] = {}
printer['gcode_macro axes_map_calibration'] = {}
printer['gcode_macro compare_belts_responses'] = {}
printer['gcode_macro axes_shaper_calibration'] = {}
printer['gcode_macro create_vibrations_profile'] = {}
printer['gcode_macro _STATUS_VARIABLES'].printer_status = READY
printer['gcode_macro _STATUS_VARIABLES'].status_effect_macros = ['_STATUS_CONSOLE', '_STATUS_KLIPPER_SCREEN']
printer['gcode_macro SET_STATUS'] = {}
printer['gcode_macro RESET_STATUS'] = {}
printer['gcode_macro _EFFECT_STATUS'] = {}
printer['gcode_macro _STATUS_CONSOLE'] = {}
printer['gcode_macro _STATUS_KLIPPER_SCREEN'] = {}
printer['gcode_macro M24'] = {}
printer['gcode_macro M25'] = {}
printer['gcode_macro Z_TILT_ADJUST'] = {}
printer['gcode_macro TURN_OFF_HEATERS'] = {}
printer['gcode_macro SET_HEATER_TEMPERATURE'] = {}
printer['gcode_macro M190'] = {}
printer['gcode_macro G28'] = {}
printer['gcode_macro BED_MESH_CALIBRATE'] = {}
printer['gcode_macro Calibrate_Hotend'] = {}
printer['gcode_macro Calibrate_BedHeater'] = {}
printer['gcode_macro TEST_SPEED'] = {}
printer['gcode_macro DUMP_VARIABLES'] = {}
printer['gcode_macro _START_PRINT'] = {}
printer['gcode_macro PRINT_START'] = {}
printer['gcode_macro _END_PRINT'] = {}
printer['gcode_macro PRINT_END'] = {}
printer['gcode_macro HOME_IF_NEEDED'] = {}
printer['gcode_macro PAUSE'].extrude = 1.0
printer['gcode_macro RESUME'].last_extruder_temp = {'restore': False, 'temp': 0}
printer['gcode_macro RESUME'].restore_idle_timeout = 0
printer['gcode_macro RESUME'].idle_state = False
printer['gcode_macro CANCEL_PRINT'].park = True
printer['gcode_macro LOAD_FILAMENT'].load_distance = 50
printer['gcode_macro LOAD_FILAMENT'].purge_distance = 25
printer['gcode_macro UNLOAD_FILAMENT'].unload_distance = 50
printer['gcode_macro UNLOAD_FILAMENT'].purge_distance = 25
printer['gcode_macro DRAW_PRIMING_LINES'] = {}
printer['gcode_macro HEAT_SOAK'].target_chamber_temp = 0
printer['gcode_macro HEAT_SOAK'].target_bed_temp = 0
printer['gcode_macro HEAT_SOAK'].stage = None
printer['gcode_macro HEAT_SOAK'].check_interval = 10
printer['gcode_macro HEAT_SOAK'].soak_time_remaining = 0
printer['gcode_macro HEAT_SOAK'].total_time_elapsed = 0
printer['gcode_macro CANCEL_HEAT_SOAK'] = {}
printer['gcode_macro _SOAK_COMPLETE'] = {}
printer['gcode_macro Razzle_Dazzle'] = {}
printer['gcode_macro LED_STOP'] = {}
printer['stepper_enable'].steppers = {'stepper_x': False, 'stepper_x1': False, 'stepper_y': False, 'stepper_y1': False, 'stepper_z': False, 'stepper_z1': False, 'stepper_z2': False, 'extruder': False}
printer['tmc5160 stepper_x'].mcu_phase_offset = 115
printer['tmc5160 stepper_x'].phase_offset_position = 0.71875
printer['tmc5160 stepper_x'].run_current = 1.196925541070979
printer['tmc5160 stepper_x'].hold_current = 1.196925541070979
printer['tmc5160 stepper_x'].drv_status = None
printer['tmc5160 stepper_x'].temperature = None
printer['tmc5160 stepper_x1'].mcu_phase_offset = 113
printer['tmc5160 stepper_x1'].phase_offset_position = 0.70625
printer['tmc5160 stepper_x1'].run_current = 1.196925541070979
printer['tmc5160 stepper_x1'].hold_current = 1.196925541070979
printer['tmc5160 stepper_x1'].drv_status = None
printer['tmc5160 stepper_x1'].temperature = None
printer['tmc5160 stepper_y'].mcu_phase_offset = 5
printer['tmc5160 stepper_y'].phase_offset_position = 0.03125
printer['tmc5160 stepper_y'].run_current = 1.196925541070979
printer['tmc5160 stepper_y'].hold_current = 1.196925541070979
printer['tmc5160 stepper_y'].drv_status = None
printer['tmc5160 stepper_y'].temperature = None
printer['tmc5160 stepper_y1'].mcu_phase_offset = 113
printer['tmc5160 stepper_y1'].phase_offset_position = 0.70625
printer['tmc5160 stepper_y1'].run_current = 1.196925541070979
printer['tmc5160 stepper_y1'].hold_current = 1.196925541070979
printer['tmc5160 stepper_y1'].drv_status = None
printer['tmc5160 stepper_y1'].temperature = None
printer['tmc2209 stepper_z'].mcu_phase_offset = 3
printer['tmc2209 stepper_z'].phase_offset_position = 0.00375
printer['tmc2209 stepper_z'].run_current = 0.7954951288348658
printer['tmc2209 stepper_z'].hold_current = 0.7954951288348658
printer['tmc2209 stepper_z'].drv_status = None
printer['tmc2209 stepper_z'].temperature = None
printer['tmc2209 stepper_z1'].mcu_phase_offset = 23
printer['tmc2209 stepper_z1'].phase_offset_position = 0.02875
printer['tmc2209 stepper_z1'].run_current = 0.7954951288348658
printer['tmc2209 stepper_z1'].hold_current = 0.7954951288348658
printer['tmc2209 stepper_z1'].drv_status = None
printer['tmc2209 stepper_z1'].temperature = None
printer['tmc2209 stepper_z2'].mcu_phase_offset = 45
printer['tmc2209 stepper_z2'].phase_offset_position = 0.05625
printer['tmc2209 stepper_z2'].run_current = 0.7954951288348658
printer['tmc2209 stepper_z2'].hold_current = 0.7954951288348658
printer['tmc2209 stepper_z2'].drv_status = None
printer['tmc2209 stepper_z2'].temperature = None
printer['heaters'].available_heaters = ['heater_bed', 'extruder']
printer['heaters'].available_sensors = ['heater_bed', 'temperature_sensor MCU_THB', 'temperature_sensor cartographer_coil', 'temperature_sensor MCU_Carto', 'temperature_sensor MCU_Manta', 'temperature_sensor CM4', 'temperature_sensor Chamber_Top', 'temperature_sensor Chamber_Bottom', 'temperature_fan Electronics_Bay', 'extruder']
printer['heaters'].available_monitors = []
printer['heater_bed'].temperature = 30.04
printer['heater_bed'].target = 0.0
printer['heater_bed'].power = 0.0
printer['idle_timeout'].state = Ready
printer['idle_timeout'].printing_time = 0.0
printer['bed_mesh'].profile_name = 
printer['bed_mesh'].mesh_min = (0.0, 0.0)
printer['bed_mesh'].mesh_max = (0.0, 0.0)
printer['bed_mesh'].probed_matrix = [[]]
printer['bed_mesh'].mesh_matrix = [[]]
printer['bed_mesh'].profiles = {'default': {'points': ((0.154081, 0.138515, 0.128514, 0.127286, 0.124611, 0.114976, 0.105323, 0.100381, 0.095501, 0.088223, 0.086316, 0.085472, 0.082817, 0.083355, 0.082789, 0.08271, 0.083689, 0.085854, 0.085431, 0.097041, 0.09809, 0.082782, 0.076187, 0.076704, 0.080354, 0.082368, 0.085072, 0.084998, 0.09281, 0.098247), (0.13349, 0.117937, 0.107106, 0.107869, 0.105265, 0.097492, 0.089134, 0.086115, 0.083736, 0.078401, 0.076131, 0.076578, 0.074993, 0.074432, 0.073981, 0.073279, 0.076415, 0.07786, 0.076497, 0.080914, 0.079868, 0.073734, 0.067697, 0.06861, 0.074403, 0.0765, 0.076991, 0.07827, 0.084321, 0.091174), (0.115153, 0.098506, 0.090259, 0.089704, 0.089289, 0.081915, 0.074853, 0.071522, 0.070107, 0.065352, 0.064095, 0.064348, 0.063359, 0.063366, 0.062642, 0.063839, 0.066829, 0.068882, 0.065567, 0.06692, 0.067317, 0.063808, 0.061525, 0.062077, 0.067504, 0.069902, 0.071985, 0.0708, 0.075848, 0.082893), (0.10113, 0.086481, 0.078463, 0.078585, 0.076577, 0.071908, 0.064862, 0.062894, 0.061941, 0.057754, 0.058218, 0.057739, 0.056563, 0.057985, 0.058215, 0.060155, 0.063841, 0.064475, 0.061995, 0.06148, 0.062291, 0.062998, 0.059635, 0.060198, 0.063275, 0.064351, 0.064443, 0.064313, 0.068566, 0.07684), (0.087541, 0.072778, 0.064184, 0.065004, 0.064873, 0.059972, 0.054762, 0.052682, 0.05196, 0.047814, 0.048828, 0.048662, 0.047562, 0.049298, 0.05166, 0.054191, 0.056344, 0.058185, 0.055904, 0.056399, 0.058255, 0.059901, 0.057071, 0.054381, 0.057025, 0.058295, 0.060332, 0.060621, 0.065348, 0.073099), (0.076249, 0.062819, 0.053624, 0.055862, 0.054496, 0.050816, 0.045956, 0.044959, 0.043136, 0.040711, 0.040648, 0.042376, 0.041509, 0.04334, 0.046139, 0.048318, 0.050896, 0.052638, 0.051177, 0.052489, 0.054141, 0.055149, 0.052769, 0.050834, 0.053905, 0.056741, 0.057701, 0.057651, 0.060949, 0.068539), (0.062961, 0.050003, 0.042626, 0.044175, 0.044124, 0.039643, 0.034897, 0.032188, 0.032766, 0.030587, 0.030765, 0.031886, 0.032234, 0.033973, 0.036233, 0.038439, 0.041461, 0.043682, 0.043368, 0.044404, 0.045898, 0.047175, 0.045166, 0.044991, 0.048977, 0.050045, 0.051778, 0.050844, 0.05529, 0.062374), (0.050956, 0.04027, 0.033325, 0.035846, 0.035244, 0.031334, 0.026306, 0.025226, 0.022973, 0.019468, 0.021434, 0.024476, 0.023603, 0.024671, 0.028464, 0.030719, 0.03295, 0.035847, 0.035952, 0.037084, 0.038658, 0.039311, 0.037685, 0.036902, 0.041278, 0.043631, 0.044393, 0.045236, 0.048815, 0.058303), (0.042713, 0.032021, 0.025363, 0.026581, 0.026737, 0.023311, 0.019686, 0.016966, 0.014918, 0.011864, 0.012528, 0.015007, 0.014918, 0.01645, 0.019827, 0.023127, 0.026422, 0.029085, 0.029146, 0.028604, 0.03021, 0.031067, 0.031046, 0.031195, 0.034584, 0.037746, 0.038255, 0.03809, 0.043406, 0.051717), (0.03986, 0.027453, 0.021182, 0.022863, 0.022917, 0.020912, 0.01716, 0.014123, 0.010975, 0.00663, 0.007801, 0.009332, 0.009895, 0.013073, 0.017622, 0.019646, 0.02271, 0.025533, 0.02431, 0.024447, 0.025183, 0.02736, 0.026544, 0.028668, 0.03153, 0.033611, 0.03387, 0.034482, 0.038883, 0.047113), (0.03519, 0.023166, 0.01715, 0.019101, 0.01973, 0.017829, 0.013489, 0.010821, 0.007301, 0.002813, 0.002036, 0.004343, 0.00592, 0.008692, 0.012491, 0.015445, 0.018081, 0.020673, 0.019302, 0.020547, 0.022027, 0.022169, 0.023651, 0.024614, 0.029264, 0.028477, 0.029462, 0.030909, 0.035955, 0.04464), (0.033921, 0.021988, 0.016127, 0.020017, 0.019997, 0.016388, 0.01213, 0.009062, 0.005651, 6.3e-05, 0.000562, 0.003104, 0.004318, 0.007276, 0.010945, 0.013736, 0.01723, 0.018198, 0.018597, 0.020125, 0.020377, 0.022048, 0.024396, 0.024846, 0.028748, 0.028733, 0.030112, 0.032135, 0.036788, 0.044542), (0.028808, 0.017942, 0.01169, 0.014128, 0.015093, 0.012077, 0.00919, 0.004887, 0.000938, -0.003359, -0.002585, 0.000434, 0.001961, 0.005127, 0.008239, 0.010209, 0.014649, 0.015873, 0.015798, 0.016549, 0.01913, 0.0219, 0.024279, 0.025609, 0.029862, 0.030183, 0.032042, 0.033011, 0.037531, 0.044496), (0.025406, 0.013062, 0.005861, 0.008686, 0.008794, 0.006143, 0.001285, -0.002287, -0.005018, -0.008235, -0.007544, -0.003896, -0.001625, 0.001842, 0.004821, 0.008042, 0.011677, 0.013234, 0.011671, 0.014442, 0.017085, 0.020866, 0.021648, 0.025144, 0.029767, 0.0306, 0.031196, 0.033438, 0.037162, 0.043925), (0.018291, 0.003178, -0.00167, 0.001088, 0.000339, -0.004234, -0.009113, -0.012708, -0.013906, -0.015547, -0.014544, -0.010613, -0.007343, -0.005425, -0.001451, 0.001954, 0.005816, 0.006086, 0.005187, 0.008722, 0.011897, 0.014608, 0.017355, 0.021177, 0.02668, 0.02721, 0.028475, 0.030401, 0.03505, 0.040087), (0.017694, 0.000862, -0.003867, -0.00199, -0.003857, -0.008963, -0.014916, -0.017121, -0.0191, -0.019156, -0.015733, -0.009463, -0.007295, -0.006527, -0.004802, -0.001575, 0.001832, 0.003353, 0.00276, 0.006186, 0.010032, 0.013781, 0.016525, 0.020997, 0.025907, 0.026782, 0.028688, 0.030938, 0.033691, 0.040304), (0.008715, -0.001131, -0.005699, -0.006195, -0.008356, -0.013533, -0.018623, -0.021585, -0.023171, -0.024161, -0.018911, -0.008744, -0.004454, -0.00802, -0.009078, -0.008268, -0.003879, 3.4e-05, -0.000406, 0.001825, 0.005859, 0.009652, 0.012471, 0.017179, 0.022335, 0.023018, 0.026626, 0.029443, 0.032763, 0.035835), (0.008274, -0.00099, -0.008056, -0.008018, -0.010108, -0.014272, -0.018827, -0.022741, -0.02565, -0.024958, -0.019618, -0.009572, -0.004552, -0.007916, -0.012686, -0.012889, -0.007048, -0.001976, -0.003257, 0.000104, 0.003542, 0.006774, 0.009599, 0.014535, 0.020588, 0.021936, 0.02448, 0.028271, 0.032398, 0.033991), (0.008315, 0.000582, -0.008875, -0.00924, -0.009743, -0.015755, -0.020064, -0.024531, -0.026437, -0.025872, -0.022057, -0.01491, -0.010529, -0.012682, -0.014965, -0.013233, -0.007844, -0.003618, -0.003326, -0.000828, 0.001737, 0.004814, 0.007177, 0.012378, 0.019155, 0.01982, 0.023087, 0.027581, 0.033457, 0.033783), (0.009523, 0.003473, -0.008115, -0.009245, -0.010755, -0.015591, -0.020276, -0.02325, -0.027218, -0.026424, -0.022154, -0.016867, -0.014393, -0.014842, -0.013763, -0.011267, -0.006677, -0.002664, -0.002306, 8.5e-05, 0.000489, 0.003716, 0.005988, 0.01095, 0.017757, 0.019296, 0.022791, 0.028289, 0.034492, 0.037796), (0.008434, 0.003305, -0.009813, -0.011842, -0.014029, -0.017993, -0.022437, -0.024681, -0.027198, -0.028758, -0.024359, -0.021006, -0.019153, -0.017266, -0.015369, -0.013864, -0.007576, -0.004697, -0.005338, -0.004207, -0.003751, -0.001329, 0.001872, 0.006328, 0.012848, 0.014878, 0.017751, 0.024865, 0.032573, 0.037275), (0.009409, 0.00483, -0.010134, -0.012979, -0.013999, -0.017017, -0.021707, -0.023399, -0.025937, -0.027401, -0.025787, -0.023583, -0.021286, -0.018405, -0.015728, -0.013021, -0.007507, -0.003813, -0.005274, -0.005105, -0.003882, -0.00076, 0.0014, 0.006236, 0.013575, 0.013793, 0.016928, 0.023542, 0.033651, 0.040292), (0.012681, 0.00365, -0.011519, -0.013592, -0.013007, -0.016088, -0.020317, -0.021148, -0.023677, -0.02675, -0.025591, -0.022852, -0.02182, -0.017047, -0.013421, -0.010105, -0.003187, -0.001311, -0.002738, -0.00097, 0.000578, 0.00237, 0.004994, 0.010895, 0.016466, 0.017294, 0.019258, 0.028104, 0.037919, 0.04492), (0.023053, 0.007329, -0.007665, -0.008696, -0.008199, -0.011085, -0.015024, -0.01646, -0.0193, -0.022497, -0.021682, -0.020567, -0.017431, -0.012789, -0.007704, -0.002037, 0.003866, 0.00625, 0.004982, 0.005306, 0.006662, 0.009518, 0.011527, 0.016232, 0.020107, 0.021472, 0.024146, 0.031093, 0.041812, 0.050079), (0.029288, 0.009673, -0.004443, -0.005567, -0.004605, -0.00621, -0.010185, -0.012755, -0.015566, -0.018724, -0.018666, -0.016853, -0.013916, -0.008459, -0.002019, 0.003235, 0.009409, 0.013119, 0.011229, 0.010323, 0.010575, 0.01215, 0.014287, 0.017538, 0.022219, 0.022162, 0.023755, 0.031374, 0.042052, 0.04916), (0.03452, 0.016344, 0.00247, 0.002003, 0.004102, 0.002468, -0.000679, -0.00163, -0.004204, -0.008491, -0.009158, -0.007186, -0.004222, 0.000618, 0.008471, 0.013685, 0.018326, 0.02099, 0.018952, 0.01761, 0.016439, 0.018096, 0.018612, 0.021467, 0.026018, 0.024606, 0.026504, 0.033649, 0.043138, 0.049695), (0.040989, 0.023426, 0.01073, 0.010593, 0.012624, 0.010471, 0.008444, 0.009828, 0.007719, 0.00222, 0.001497, 0.003871, 0.006004, 0.010458, 0.016901, 0.022482, 0.026374, 0.02761, 0.024551, 0.02344, 0.021441, 0.022861, 0.022914, 0.02577, 0.028328, 0.027841, 0.027552, 0.034131, 0.043074, 0.048597), (0.054196, 0.036317, 0.022173, 0.022984, 0.02461, 0.023046, 0.0211, 0.022848, 0.021239, 0.015733, 0.014907, 0.017676, 0.020253, 0.024232, 0.028896, 0.033068, 0.037739, 0.039009, 0.035866, 0.03322, 0.03219, 0.032375, 0.033207, 0.032898, 0.034894, 0.033152, 0.03361, 0.039576, 0.047877, 0.053834), (0.069154, 0.049538, 0.034101, 0.033598, 0.035192, 0.034897, 0.033264, 0.033966, 0.032399, 0.026413, 0.025919, 0.029939, 0.032117, 0.035207, 0.039697, 0.043255, 0.047065, 0.04902, 0.044302, 0.042012, 0.040376, 0.041479, 0.0402, 0.03959, 0.03976, 0.037849, 0.038269, 0.044078, 0.052012, 0.057973), (0.092874, 0.067424, 0.048158, 0.047359, 0.048967, 0.048404, 0.046286, 0.047192, 0.045016, 0.039761, 0.039884, 0.043235, 0.046178, 0.04911, 0.053155, 0.056352, 0.060047, 0.059708, 0.05387, 0.051188, 0.050336, 0.049519, 0.047828, 0.047118, 0.048008, 0.045242, 0.045325, 0.049244, 0.056162, 0.063266)), 'mesh_params': OrderedDict([('min_x', 30.0), ('max_x', 320.0), ('min_y', 30.0), ('max_y', 320.0), ('x_count', 30), ('y_count', 30), ('mesh_x_pps', 2), ('mesh_y_pps', 2), ('algo', 'bicubic'), ('tension', 0.2)])}}
printer['z_tilt'].applied = False
printer['gcode_macro PROBECALIBRATE'] = {}
printer['gcode_macro G32'] = {}
printer['tmc2209 extruder'].mcu_phase_offset = 3
printer['tmc2209 extruder'].phase_offset_position = 0.00492875
printer['tmc2209 extruder'].run_current = 0.6119193298729737
printer['tmc2209 extruder'].hold_current = 0.6119193298729737
printer['tmc2209 extruder'].drv_status = None
printer['tmc2209 extruder'].temperature = None
printer['fan_generic Part_Fan'].speed = 0.0
printer['fan_generic Part_Fan'].rpm = None
printer['heater_fan Hotend_Fan'].speed = 0.0
printer['heater_fan Hotend_Fan'].rpm = None
printer['temperature_sensor MCU_THB'].temperature = 35.55
printer['temperature_sensor MCU_THB'].measured_min_temp = 35.51
printer['temperature_sensor MCU_THB'].measured_max_temp = 35.87
printer['neopixel th_led'].color_data = [(1.0, 1.0, 1.0, 0.0), (1.0, 1.0, 1.0, 0.0), (1.0, 1.0, 1.0, 0.0)]
printer['mcu scanner'].mcu_version = CARTOGRAPHER 5.1.0
printer['mcu scanner'].mcu_build_versions = 
printer['mcu scanner'].mcu_constants = {'ADC_MAX': 4095, 'BUS_PINS_i2c1': 'PB6,PB7', 'BUS_PINS_spi1': 'PA6,PA7,PA5', 'CANBUS_FREQUENCY': 1000000, 'CARTOGRAPHER_ADC_SMOOTH_COUNT': 16, 'CLOCK_FREQ': 48000000, 'MCU': 'stm32f042x6', 'PWM_MAX': 2, 'RECEIVE_WINDOW': 192, 'RESERVE_PINS_CAN': 'PA11,PA12', 'RESERVE_PINS_crystal': 'PF0,PF1', 'STATS_SUMSQ_BASE': 256, 'STEPPER_BOTH_EDGE': 1}
printer['mcu scanner'].last_stats = {'mcu_awake': 0.028, 'mcu_task_avg': 1.1e-05, 'mcu_task_stddev': 2.5e-05, 'bytes_write': 778, 'bytes_read': 4788, 'bytes_retransmit': 0, 'bytes_invalid': 0, 'send_seq': 105, 'receive_seq': 105, 'retransmit_seq': 0, 'srtt': 0.001, 'rttvar': 0.0, 'rto': 0.025, 'ready_bytes': 0, 'upcoming_bytes': 0, 'freq': 47998746, 'adj': 47999867}
printer['probe'].name = scanner
printer['probe'].last_z_result = 0.0
printer['temperature_sensor cartographer_coil'].temperature = 27.72
printer['temperature_sensor cartographer_coil'].measured_min_temp = 27.67
printer['temperature_sensor cartographer_coil'].measured_max_temp = 27.79
printer['scanner'].last_sample = None
printer['scanner'].last_received_sample = {'clock': 882534492, 'data': 33416825, 'temp': 27.723019263206993, '#name': 'cartographer_data', '#sent_time': 53.106367746, '#receive_time': 53.451946227, 'time': 18.37258092810722, 'data_smooth': 33417051.235561542, 'freq': 2987717.202505011}
printer['scanner'].model = default
printer['temperature_sensor MCU_Carto'].temperature = 38.85
printer['temperature_sensor MCU_Carto'].measured_min_temp = 37.93
printer['temperature_sensor MCU_Carto'].measured_max_temp = 39.32
printer['gcode_macro PROBE_CALIBRATE'] = {}
printer['gcode_macro DATA_SAMPLE'] = {}
printer['motors_sync'].applied = False
printer['temperature_sensor MCU_Manta'].temperature = 52.21
printer['temperature_sensor MCU_Manta'].measured_min_temp = 52.11
printer['temperature_sensor MCU_Manta'].measured_max_temp = 52.81
printer['temperature_host CM4'].temperature = 50.63
printer['temperature_sensor CM4'].temperature = 50.63
printer['temperature_sensor CM4'].measured_min_temp = 50.15
printer['temperature_sensor CM4'].measured_max_temp = 52.09
printer['temperature_sensor Chamber_Top'].temperature = 26.96
printer['temperature_sensor Chamber_Top'].measured_min_temp = 26.93
printer['temperature_sensor Chamber_Top'].measured_max_temp = 27.04
printer['temperature_sensor Chamber_Bottom'].temperature = 25.34
printer['temperature_sensor Chamber_Bottom'].measured_min_temp = 25.34
printer['temperature_sensor Chamber_Bottom'].measured_max_temp = 25.54
printer['temperature_fan Electronics_Bay'].speed = 1.0
printer['temperature_fan Electronics_Bay'].rpm = None
printer['temperature_fan Electronics_Bay'].temperature = 37.58
printer['temperature_fan Electronics_Bay'].target = 30.0
printer['controller_fan Driver_Fan'].speed = 0.0
printer['controller_fan Driver_Fan'].rpm = None
printer['fan_generic Bed_Fan'].speed = 0.0
printer['fan_generic Bed_Fan'].rpm = None
printer['fan_generic Fume_Fan'].speed = 0.0
printer['fan_generic Fume_Fan'].rpm = None
printer['gcode_macro M106'] = {}
printer['gcode_macro _LED_STATUS_OFF_TH'] = {}
printer['gcode_macro _STATUS_TH_LED'] = {}
printer['gcode_macro _LED_STATUS_IDLE_TH'] = {}
printer['gcode_macro _LED_STATUS_READY_TH'] = {}
printer['gcode_macro _LED_STATUS_PRINTING_TH'] = {}
printer['neopixel chamber'].color_data = [(1.0, 1.0, 1.0, 0.0), (1.0, 1.0, 1.0, 0.0), (1.0, 1.0, 1.0, 0.0), (1.0, 1.0, 1.0, 0.0), (1.0, 1.0, 1.0, 0.0), (1.0, 1.0, 1.0, 0.0), (1.0, 1.0, 1.0, 0.0), (1.0, 1.0, 1.0, 0.0), (1.0, 1.0, 1.0, 0.0), (1.0, 1.0, 1.0, 0.0), (1.0, 1.0, 1.0, 0.0), (1.0, 1.0, 1.0, 0.0), (1.0, 1.0, 1.0, 0.0), (1.0, 1.0, 1.0, 0.0), (1.0, 1.0, 1.0, 0.0), (1.0, 1.0, 1.0, 0.0), (1.0, 1.0, 1.0, 0.0), (1.0, 1.0, 1.0, 0.0), (1.0, 1.0, 1.0, 0.0), (1.0, 1.0, 1.0, 0.0), (1.0, 1.0, 1.0, 0.0), (1.0, 1.0, 1.0, 0.0), (1.0, 1.0, 1.0, 0.0), (1.0, 1.0, 1.0, 0.0), (1.0, 1.0, 1.0, 0.0), (1.0, 1.0, 1.0, 0.0), (1.0, 1.0, 1.0, 0.0), (1.0, 1.0, 1.0, 0.0), (1.0, 1.0, 1.0, 0.0), (1.0, 1.0, 1.0, 0.0), (1.0, 1.0, 1.0, 0.0), (1.0, 1.0, 1.0, 0.0), (1.0, 1.0, 1.0, 0.0), (1.0, 1.0, 1.0, 0.0), (1.0, 1.0, 1.0, 0.0), (1.0, 1.0, 1.0, 0.0), (1.0, 1.0, 1.0, 0.0), (1.0, 1.0, 1.0, 0.0), (1.0, 1.0, 1.0, 0.0), (1.0, 1.0, 1.0, 0.0), (1.0, 1.0, 1.0, 0.0), (1.0, 1.0, 1.0, 0.0), (1.0, 1.0, 1.0, 0.0), (1.0, 1.0, 1.0, 0.0), (1.0, 1.0, 1.0, 0.0), (1.0, 1.0, 1.0, 0.0), (1.0, 1.0, 1.0, 0.0), (1.0, 1.0, 1.0, 0.0), (1.0, 1.0, 1.0, 0.0), (1.0, 1.0, 1.0, 0.0), (1.0, 1.0, 1.0, 0.0), (1.0, 1.0, 1.0, 0.0), (1.0, 1.0, 1.0, 0.0), (1.0, 1.0, 1.0, 0.0), (1.0, 1.0, 1.0, 0.0), (1.0, 1.0, 1.0, 0.0), (1.0, 1.0, 1.0, 0.0), (1.0, 1.0, 1.0, 0.0), (1.0, 1.0, 1.0, 0.0), (1.0, 1.0, 1.0, 0.0), (1.0, 1.0, 1.0, 0.0), (1.0, 1.0, 1.0, 0.0), (1.0, 1.0, 1.0, 0.0), (1.0, 1.0, 1.0, 0.0), (1.0, 1.0, 1.0, 0.0), (1.0, 1.0, 1.0, 0.0), (1.0, 1.0, 1.0, 0.0), (1.0, 1.0, 1.0, 0.0), (1.0, 1.0, 1.0, 0.0), (1.0, 1.0, 1.0, 0.0), (1.0, 1.0, 1.0, 0.0), (1.0, 1.0, 1.0, 0.0)]
printer['gcode_macro LED_OFF'] = {}
printer['gcode_macro LED_ON'] = {}
printer['gcode_macro _STATUS_CHAMBER_LED'] = {}
printer['gcode_macro _LED_STATUS_IDLE'] = {}
printer['gcode_macro _LED_STATUS_READY'] = {}
printer['gcode_macro _LED_STATUS_PRINTING'] = {}
printer['gcode_macro _LED_Rainbow'] = {}
printer['gcode_macro _LED_RainbowGreg'] = {}
printer['gcode_macro _LED_Epilepsie'] = {}
printer['gcode_macro _LED_Commet'] = {}
printer['gcode_macro _LED_DoubleCommet'] = {}
printer['gcode_macro LED_KITT'] = {}
printer['gcode_macro _LED_Pacman'] = {}
printer['gcode_macro _LED_White'] = {}
printer['pause_resume'].is_paused = False
printer['gcode_macro SET_PAUSE_NEXT_LAYER'] = {}
printer['gcode_macro SET_PAUSE_AT_LAYER'] = {}
printer['gcode_macro SET_PRINT_STATS_INFO'].pause_next_layer = {'enable': False, 'call': 'PAUSE'}
printer['gcode_macro SET_PRINT_STATS_INFO'].pause_at_layer = {'enable': False, 'layer': 0, 'call': 'PAUSE'}
printer['gcode_macro _TOOLHEAD_PARK_PAUSE_CANCEL'] = {}
printer['gcode_macro _CLIENT_EXTRUDE'] = {}
printer['gcode_macro _CLIENT_RETRACT'] = {}
printer['gcode_macro _CLIENT_LINEAR_MOVE'] = {}
printer['gcode_macro SET_ACTIVE_SPOOL'] = {}
printer['gcode_macro CLEAR_ACTIVE_SPOOL'] = {}
printer['gcode_macro GET_TIMELAPSE_SETUP'] = {}
printer['gcode_macro _SET_TIMELAPSE_SETUP'] = {}
printer['gcode_macro TIMELAPSE_TAKE_FRAME'].enable = True
printer['gcode_macro TIMELAPSE_TAKE_FRAME'].takingframe = False
printer['gcode_macro TIMELAPSE_TAKE_FRAME'].park = {'enable': False, 'pos': 'back_left', 'time': 0.1, 'custom': {'x': 10.0, 'y': 10.0, 'dz': 0.0}, 'coord': {'x': 0.0, 'y': 360.0, 'dz': 0}}
printer['gcode_macro TIMELAPSE_TAKE_FRAME'].extruder = {'fw_retract': False, 'retract': 1.0, 'extrude': 1.0}
printer['gcode_macro TIMELAPSE_TAKE_FRAME'].speed = {'travel': 100.0, 'retract': 15.0, 'extrude': 15.0}
printer['gcode_macro TIMELAPSE_TAKE_FRAME'].verbose = False
printer['gcode_macro TIMELAPSE_TAKE_FRAME'].check_time = 0.5
printer['gcode_macro TIMELAPSE_TAKE_FRAME'].restore = {'absolute': {'coordinates': True, 'extrude': True}, 'speed': 1500, 'e': 0, 'factor': {'speed': 1.0, 'extrude': 1.0}}
printer['gcode_macro TIMELAPSE_TAKE_FRAME'].macro = {'pause': 'PAUSE_BASE', 'resume': 'RESUME_BASE'}
printer['gcode_macro TIMELAPSE_TAKE_FRAME'].is_paused = False
printer['gcode_macro _TIMELAPSE_NEW_FRAME'] = {}
printer['gcode_macro HYPERLAPSE'].cycle = 0
printer['gcode_macro HYPERLAPSE'].run = False
printer['gcode_macro TIMELAPSE_RENDER'].render = False
printer['gcode_macro TIMELAPSE_RENDER'].run_identifier = 0
printer['gcode_macro TEST_STREAM_DELAY'] = {}
printer['motion_report'].live_position = Coord(x=0.0, y=0.0, z=0.0, e=0.0)
printer['motion_report'].live_velocity = 0.0
printer['motion_report'].live_extruder_velocity = 0.0
printer['motion_report'].steppers = ['extruder', 'stepper_x', 'stepper_x1', 'stepper_y', 'stepper_y1', 'stepper_z', 'stepper_z1', 'stepper_z2']
printer['motion_report'].trapq = ['extruder', 'toolhead']
printer['query_endstops'].last_query = {}
printer['system_stats'].sysload = 1.814453125
printer['system_stats'].cputime = 12.359267945
printer['system_stats'].memavail = 3181204
printer['manual_probe'].is_active = False
printer['manual_probe'].z_position = None
printer['manual_probe'].z_position_lower = None
printer['manual_probe'].z_position_upper = None
printer['toolhead'].homed_axes = 
printer['toolhead'].axis_minimum = Coord(x=0.0, y=0.0, z=-5.0, e=0.0)
printer['toolhead'].axis_maximum = Coord(x=350.0, y=360.0, z=245.0, e=0.0)
printer['toolhead'].print_time = 10.684525495
printer['toolhead'].stalls = 0
printer['toolhead'].estimated_print_time = 18.39811128
printer['toolhead'].extruder = extruder
printer['toolhead'].position = Coord(x=0.0, y=0.0, z=0.0, e=0.0)
printer['toolhead'].max_velocity = 1000.0
printer['toolhead'].max_accel = 12000.0
printer['toolhead'].minimum_cruise_ratio = 0.5
printer['toolhead'].square_corner_velocity = 5.0
printer['extruder'].temperature = 28.34
printer['extruder'].target = 0.0
printer['extruder'].power = 0.0
printer['extruder'].can_extrude = False
printer['extruder'].pressure_advance = 0.04
printer['extruder'].smooth_time = 0.04
printer['extruder'].motion_queue = None

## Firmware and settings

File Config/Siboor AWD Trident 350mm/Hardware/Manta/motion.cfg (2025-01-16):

#####################################################################
##                     Model and Acceleration
#####################################################################
[printer]								# Printer configuration
kinematics: corexy						# Printer type: corexy
max_velocity: 1000						# Maximum velocity (original 600)
max_accel: 12000						# Maximum acceleration (original 10000)
max_z_velocity: 50						# Maximum Z-axis velocity
max_z_accel: 100						# Maximum Z-axis acceleration
minimum_cruise_ratio: 0.5				# Default 0.5
square_corner_velocity: 12				# Square corner velocity (orginal 25, Klipper recommended 5) setting to 12 so Orca can use 9/12


#####################################################################
##                            X Axis
#####################################################################

# Motors are SIBOOR-42STH48-2504(S45) 2 phase 1.8' 0.9-ohm 2.5A 1.6mH
[stepper_x]
step_pin: PE6                         	# X-axis motor pulse pin setting
dir_pin: !PE5                         	# X-axis motor direction pin setting
enable_pin: !PC14                     	# X-axis motor enable pin setting
microsteps: 32                        	# Motor microsteps setting
rotation_distance: 40                 	# Active pulley circumference mm (2GT-20T pulley 40, 2GT-16T pulley 32)
full_steps_per_rotation: 200          	# Number of pulses required for a single motor revolution (1.8 degree motor: 200, 0.9 degree motor: 400)
endstop_pin: PF4						# Use Manta Endstop 0 dummy for now when no TH plugged in.  This will get REDEFINED in the relevant toolhead.cfg LATER (if included)
position_min: 0                       	# X-axis minimum travel - software limit
position_endstop: 350                	# Mechanical reset point coordinates for X-axis
position_max: 350                     	# X-axis maximum travel - software limit
homing_speed: 150                     	# Homing speed maximum 100
homing_retract_dist: 5                	# Setback distance after the first trigger of the homing switch
homing_positive_dir: true             	# Direction of homing (generally no change required)

[tmc5160 stepper_x]
cs_pin: PC13                          	# Chip select pin
spi_software_sclk_pin: PG8            	# SPI clock pin
spi_software_mosi_pin: PG6            	# SPI master out slave in pin
spi_software_miso_pin: PG7            	# SPI master in slave out pin
driver_TPFD: 0                        	# Driver setting
run_current: 1.2                      	# Running current  default Siboor was 1.5
spi_speed: 3500000                    	# SPI speed
interpolate: True                     	# Interpolation

# driver tune https://github.com/MakerBogans/docs/wiki/TMC-Driver-Tuning
# and driver autotune: https://github.com/andrewmcgr/klipper_tmc_autotune
#driver_TBL: 1
#driver_TOFF: 3
#driver_HSTRT: 7
#driver_HEND: 9

# [autotune_tmc stepper_x]
# motor: siboor-42sth48-2504(s45)
# voltage: 48
# [autotune_tmc stepper_x1]
# motor: siboor-42sth48-2504(s45)
# voltage: 48
# [autotune_tmc stepper_y]
# motor: siboor-42sth48-2504(s45)
# voltage: 48
# [autotune_tmc stepper_y1]
# motor: siboor-42sth48-2504(s45)
# voltage: 48
# [autotune_tmc stepper_z]
# motor: siboor-42sth48-2504(s45)
# voltage: 24
# [autotune_tmc stepper_z1]
# motor: siboor-42sth48-2504(s45)
# voltage: 24
# [autotune_tmc stepper_z2]
# motor: siboor-42sth48-2504(s45)
# voltage: 24

[stepper_x1]
step_pin: PD4                         	# X1-axis motor pulse pin setting
dir_pin: PD3                          	# X1-axis motor direction pin setting (motors are flipped so PD3)
enable_pin: !PD6                      	# X1-axis motor enable pin setting
microsteps: 32                        	# Motor microsteps setting
rotation_distance: 40                 	# Active pulley circumference mm (2GT-20T pulley 40, 2GT-16T pulley 32)
full_steps_per_rotation: 200          	# Number of pulses required for a single motor revolution (1.8 degree motor: 200, 0.9 degree motor: 400)

[tmc5160 stepper_x1]
cs_pin: PD5                           	# Chip select pin
spi_software_sclk_pin: PG8            	# SPI clock pin
spi_software_mosi_pin: PG6            	# SPI master out slave in pin
spi_software_miso_pin: PG7            	# SPI master in slave out pin
driver_TPFD: 0                        	# Driver setting
run_current: 1.2                      	# Running current  default Siboor was 1.5
spi_speed: 3500000                    	# SPI speed
interpolate: True                     	# Interpolation


#####################################################################
##                           Y Aixs
#####################################################################

[stepper_y]
step_pin: PC7                         	# Y-axis motor pulse pin setting
dir_pin: !PC8                         	# Y-axis motor direction pin setting
enable_pin: !PD2                      	# Y-axis motor enable pin setting
microsteps: 32                        	# Motor microsteps setting
rotation_distance: 40                 	# Active pulley circumference mm (2GT-20T pulley 40, 2GT-16T pulley 32)
full_steps_per_rotation: 200          	# Number of pulses required for a single motor revolution (1.8 degree motor: 200, 0.9 degree motor: 400)
endstop_pin: PF2                      	# Manta M3
position_min: 0                       	# Y-axis minimum travel - software limit
position_endstop: 360                 	# Mechanical reset point coordinates for Y-axis (change to 350 for 350 models)
position_max: 360                     	# Y-axis maximum travel - software limit (change to 350 for 350 models)
homing_speed: 150                     	# Homing speed maximum 100
homing_retract_dist: 5                	# Setback distance after the first trigger of the homing switch
homing_positive_dir: true             	# Direction of homing (generally no change required)

[tmc5160 stepper_y]
cs_pin: PC6                           	# Chip select pin
spi_software_sclk_pin: PG8            	# SPI clock pin
spi_software_mosi_pin: PG6            	# SPI master out slave in pin
spi_software_miso_pin: PG7            	# SPI master in slave out pin
driver_TPFD: 0                        	# Driver setting
run_current: 1.2                      	# Running current  default Siboor was 1.5
spi_speed: 3500000                    	# SPI speed
interpolate: True                     	# Interpolation

[stepper_y1]
step_pin: PE2                         	# Y1-axis motor pulse pin setting
dir_pin: PE1                          	# Y1-axis motor direction pin setting (motors are flipped so PE1)
enable_pin: !PE4                      	# Y1-axis motor enable pin setting
microsteps: 32                        	# Motor microsteps setting
rotation_distance: 40                 	# Active pulley circumference mm (2GT-20T pulley 40, 2GT-16T pulley 32)
full_steps_per_rotation: 200          	# Number of pulses required for a single motor revolution (1.8 degree motor: 200, 0.9 degree motor: 400)

[tmc5160 stepper_y1]
cs_pin: PE3                           	# Chip select pin
spi_software_sclk_pin: PG8            	# SPI clock pin
spi_software_mosi_pin: PG6            	# SPI master out slave in pin
spi_software_miso_pin: PG7            	# SPI master in slave out pin
driver_TPFD: 0                        	# Driver setting
run_current: 1.2                      	# Running current  default Siboor was 1.5
spi_speed: 3500000                    	# SPI speed
interpolate: True                     	# Interpolation


#####################################################################
#    -------z1------- 
#   |                 |
#   |                 |
#   |                 |
#   |                 |
#   |                 |
#   |                 |
#  z0---   display ---z2
#####################################################################
##                  Z0 Axis
#####################################################################
[stepper_z]
step_pin: PB8                         	# Z0-axis motor pulse pin setting
dir_pin: !PB7                         	# Z0-axis motor direction pin setting
enable_pin: !PE0                      	# Z0-axis motor enable pin setting
microsteps: 16                        	# Motor microsteps setting
rotation_distance: 4                  	# Active pulley circumference mm
endstop_pin: PF3						# Dummy Manta M2 to get working without carto or toolhead.  BE CAREFUL!!
#position_endstop: 200               	# Dummy to get working without toolhead
position_max: 245                     	# Z0-axis maximum travel - software limit
position_min: -5.0                    	# Z0-axis minimum travel - software limit
homing_speed: 50                      	# Homing speed
homing_retract_dist: 0                	# Setback distance after the first trigger of the homing switch
homing_positive_dir: False            	# Direction of homing (generally no change required)
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

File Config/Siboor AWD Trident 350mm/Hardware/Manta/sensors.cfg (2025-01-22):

#####################################################################
##	                 Temperature Monitoring
#####################################################################

[temperature_sensor MCU_Manta]        	# BTT-MCU temperature sensor configuration       
sensor_type: temperature_mcu        	# Manta MCU
max_temp: 80

[temperature_sensor CM4]             	# BTT-PI temperature sensor configuration
sensor_type: temperature_host			# cm4 host
max_temp: 80

[temperature_sensor Chamber_Top]
sensor_type: Generic 3950
sensor_pin: PC5							# Manta TH1
max_temp: 75

[temperature_sensor Chamber_Bottom]
sensor_type: Generic 3950
sensor_pin: PB0							# Manta TH0
max_temp: 75

# [temperature_sensor Electronics_Bay]
# sensor_type: Generic 3950
# sensor_pin: PC4							# Manta TH2
# max_temp: 75

[filament_switch_sensor RunoutSensor]
pause_on_runout: False
#   When set to True, a PAUSE will execute immediately after a runout
#   is detected. Note that if pause_on_runout is False and the
#   runout_gcode is omitted then runout detection is disabled. Default
#   is True.
runout_gcode: PAUSE
#   A list of G-Code commands to execute after a filament runout is
#   detected. See docs/Command_Templates.md for G-Code format. If
#   pause_on_runout is set to True this G-Code will run after the
#   PAUSE is complete. The default is not to run any G-Code commands.
insert_gcode: RESUME
#   A list of G-Code commands to execute after a filament insert is
#   detected. See docs/Command_Templates.md for G-Code format. The
#   default is not to run any G-Code commands, which disables insert
#   detection.
#event_delay: 3.0
#   The minimum amount of time in seconds to delay between events.
#   Events triggered during this time period will be silently
#   ignored. The default is 3 seconds.
#pause_delay: 0.5
#   The amount of time to delay, in seconds, between the pause command
#   dispatch and execution of the runout_gcode. It may be useful to
#   increase this delay if OctoPrint exhibits strange pause behavior.
#   Default is 0.5 seconds.
switch_pin: !PC15						# Manta M6 endstop pin M6
#   The pin on which the switch is connected. This parameter must be
#   provided.

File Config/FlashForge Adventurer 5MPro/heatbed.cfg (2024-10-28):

[heater_bed]
heater_pin: PB9
sensor_type: Generic 3950
sensor_pin: PC3
pullup_resistor: 4700
#control: watermark
#max_power: 1.0
min_temp: -100
max_temp: 130

[verify_heater heater_bed]
max_error: 120
check_gain_time:200
hysteresis: 10
heating_gain: 10

#AutoCalibration                   
[bed_mesh]                         
speed: 300                          
horizontal_move_z:2
move_check_distance: 5
mesh_min: -105, -105            
mesh_max: 105, 105             
probe_count: 5, 5                  
mesh_pps: 3, 3                     
algorithm: bicubic                 
bicubic_tension: 0.2               
#fade_start: 3
#fade_end: 10
#fade_target: 0

[skew_correction]

[probe]
pin: !PB4
speed: 2
lift_speed: 5
samples: 1

[temperature_sensor Load_Cell]
sensor_type: MAX31856
sensor_pin: PD5
#spi_bus: spi4
spi_speed: 1000000
spi_software_sclk_pin: PD6
spi_software_mosi_pin: PD7
spi_software_miso_pin: PD8
min_temp: 0
max_temp: 2048
gcode_id: W

# reset the check_level_pin state
[output_pin _level_clear]
pin: PD10
value:0

# check level pin is triggered when load cell tare is set via level_h1 pin
[gcode_button _check_level_pin]
pin: !PE0
press_gcode:
    G4 P0

# set load cell tare
[output_pin _level_h1]
pin:PG2
value:0

# don't use (!) - changes load cell calibration
[output_pin _level_h2]
pin:PG3
value:0

# don't use (!) - changes load cell calibration
[output_pin _level_h3]
pin:PG4
value:0


[gcode_macro AUTO_BED_LEVEL]
description: Move to temps and initiate Bed Mesh Calibrate
gcode:
    {% set bed_temp = params.BED_TEMP|default(60)|float %}
    {% set extruder_temp = params.EXTRUDER_TEMP|default(200)|float %}
    {% set profile = params.PROFILE|default("auto") %}
    {% set NOZZLE = 150 %}  ; nozzle temp to use during bed level

    # clear old mesh and home if necessary
    BED_MESH_CLEAR
    {% if not "xyz" in printer.toolhead.homed_axes %}
        G28
    {% endif %}

    # bed heating
    G90                     ; absolute coordinates
    G1 Z10 F1800            ; raise bed
    M140 S{bed_temp - 2}	; set bed temp to lower temp just incase bed temp is already HOTTER.
    # wait for bed to reach temp, if HOTTER; don't wait for stabilization
    TEMPERATURE_WAIT SENSOR=heater_bed MAXIMUM={bed_temp}
    M140 S{bed_temp}        ; set bed temp
    # wait for bed to reach temp, don't wait for stabilization
    TEMPERATURE_WAIT SENSOR=heater_bed MINIMUM={bed_temp}
    LOAD_CELL_TARE          ; reset tare before manual probe

    # nozzle heating
    M104 S{extruder_temp}   ; set nozzle temperature
    # wait for nozzle to reach temp, don't wait for stabilization
    TEMPERATURE_WAIT SENSOR=extruder MINIMUM={extruder_temp}

    # wipe to left
    G90                     ; absolute coordinates
    G1 X50 Y110 Z5 F18000   ; get into position
    PROBE                   ; moove nozzle to bed
    G91                     ; relative position
    G1 X-40 F900            ; wipe move left

    # wipe to right
    G90                     ; absolute coordinates
    G1 X-50 Y110 Z5 F18000  ; get into position
    PROBE                   ; moove nozzle to bed
    G91                     ; relative position
    G1 X40 F900             ; wipe move right

    # wait for nozzle cooldown to calibration temp
    M106 S255               ; turn on fan
    M104 S0                 ; turn of noozle heating
    TEMPERATURE_WAIT SENSOR=extruder MAXIMUM={NOZZLE + 2}
    M104 S{NOZZLE}               ; turn nozzle heating on to 150
    M107                    ; turn off fan

    # move to remove cold filament
    G1 X10 F300

    # start the calibration
    BED_MESH_CALIBRATE PROFILE="{profile}"


[gcode_macro BED_MESH_CALIBRATE]
description: Begin bed mesh point checks
rename_existing: _BED_MESH_CALIBRATE_ORIG
gcode:
    G90                     ; absolute coordinates
    G1 Z2 F1800             ; move noozle near bed
    LOAD_CELL_TARE          ; reset tare before leveling
    _BED_MESH_CALIBRATE_ORIG {rawparams}


[gcode_macro Z_OFFSET_APPLY_ENDSTOP]
# This macro is replaced because saving the z-offset to the endstop would not have the expected outcome
# on this printer. The endstop is separate from the probe. After bed leveling before print, the offset
# would be ineffective.
rename_existing: _Z_OFFSET_APPLY_ENDSTOP
gcode:
    RESPOND MSG="Notice: z-offset should not be saved to endstop on this printer. This command runs Z_OFFSET_APPLY_PROBE instead."
    Z_OFFSET_APPLY_PROBE


[gcode_macro LOAD_CELL_TARE]
description: Zero out Load cell
variable_success: 0
gcode:
    # reset success
    SET_GCODE_VARIABLE MACRO=LOAD_CELL_TARE VARIABLE=success VALUE=0
    # try set tare, up to 10 times
    {% for i in range(10) %}
        _LOAD_CELL_TARE_IF_NO_SUCCESS
    {% endfor %}
    # final check if successfull
    _LOAD_CELL_TARE_FINAL_CHECK


[gcode_macro _LOAD_CELL_TARE_IF_NO_SUCCESS]
gcode:
    {% if not printer["gcode_macro LOAD_CELL_TARE"].success %}
        _LOAD_CELL_TARE_SET
        _LOAD_CELL_TARE_CHECK
    {% endif %}


[gcode_macro _LOAD_CELL_TARE_SET]
gcode:
    # Tare is set by toggeling _level_h1 pin
    SET_PIN PIN=_level_h1 VALUE=0
    G4 P500
    M400
    SET_PIN PIN=_level_h1 VALUE=1
    G4 P500
    M400
    SET_PIN PIN=_level_h1 VALUE=0
    G4 P500
    M400
    SET_PIN PIN=_level_h1 VALUE=1
    G4 P500
    M400


[gcode_macro _LOAD_CELL_TARE_CHECK]
gcode:
    # If level check pin is set, tare is successfull.
    {% if "PRESSED" in printer['gcode_button _check_level_pin'].state %}
        SET_GCODE_VARIABLE MACRO=LOAD_CELL_TARE VARIABLE=success VALUE=1
    {% endif %}


[gcode_macro _LOAD_CELL_TARE_FINAL_CHECK]
gcode:
    # Check success
    {% if printer["gcode_macro LOAD_CELL_TARE"].success %}
        # Toggle level clear plin.
        # No sure what the level clear pin does. But we do the same as the stock software.
        SET_PIN PIN=_level_clear VALUE=0
        G4 P10
        M400
        SET_PIN PIN=_level_clear VALUE=1
        RESPOND TYPE=echo MSG="Load cell tare success."
    # Else raise error
    {% else %}
        {action_raise_error("Load cell tare failed.")}
    {% endif %}

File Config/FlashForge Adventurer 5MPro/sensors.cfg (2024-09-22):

[temperature_sensor TVOC_Level]
sensor_type: MAX31865
sensor_pin: PD4
#spi_bus: spi4
#cs_pin: PD0
spi_speed: 500000
spi_software_sclk_pin: PE3
spi_software_mosi_pin: PE4
spi_software_miso_pin: PE5
min_temp: 0
max_temp: 2048
gcode_id: V

# Unused Filament runout sensor e1 must be configure as an input pint 
# Otherwise the runout sensor does not work
[gcode_button _e1_sensor_input]
pin: !PE1
press_gcode:
    G4 P0

# Filament runout sensor
[filament_switch_sensor runout_sensor]
pause_on_runout: False
switch_pin: !PB14
event_delay: 1.0
runout_gcode:
    _FILAMENT_RUNOUT_EVENT

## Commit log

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2024-09-20 Updated SB fan/led into stealthburner.cfg
    [fans.cfg, led.cfg, macros.cfg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]
2024-09-20 Updated Internal/External fan macro settings
    [macros-pro.cfg]
2024-09-20 Cleaned up Orca M106 to FAN macro
    [fans.cfg]
2024-09-21 Updated PRINT_START to reset to 100% flow and speed.
    [macros.cfg]
2024-09-22 New broken out include file structure
    [fans.cfg, hardware.cfg, heatbed.cfg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]
2024-09-22 Clenaed up the STATUS logic and integrated Knomi into the round robin polling status effects. Overloaded / set quite a few status points in HEAT SOAK and overloaded bunch of functions.
    [knomi.cfg, led.cfg, macros.cfg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]
2024-09-22 Cleaned up some typos on variable names and got most of HOMING and heaters off status overloads working
    [knomi.cfg, led.cfg, status.cfg]
2024-09-22 More Status changes and refining how to call it.
    [knomi.cfg, led.cfg, macros.cfg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]
2024-09-22 Updated RESET_STATUS after most of the _END type status'
    [led.cfg, macros.cfg, status.cfg]
2024-09-25 Latest test update and just small refinements
    [macros.cfg, printer.cfg, status.cfg]
2024-09-29 Updated status a bit for cleaned up HEATER_EXTRUDER
    [status.cfg]
2024-10-28 Updated for improvements on homing
    [heatbed.cfg, led.cfg, macros.cfg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]
2024-11-13 Updated Siboor Trident files for latest official files and 5160 drivers
    [Siboor Trident AWD 350 TMC2240.cfg, Siboor Trident AWD 350 TMC5160.cfg, bed.cfg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]
2024-11-19 Incorporated new Galileo2 extruder motor values
    [stealthburner.cfg, xol.cfg]
2024-12-09 Updated a BUNCH of Siboor configs
    [AWD_350_Model_TMC5160_new.cfg, Manta.cfg, Siboor Trident AWD 350 TMC2240.cfg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]
2024-12-09 Updated led config and added .conf files
    [fans.cfg, led.cfg, sensors.cfg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]
2024-12-11 Cleaned up fan controls and status/led stuff
    [Custom Siboor 350 XOL.stl, cartographer.cfg, fans.cfg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]
2024-12-12 Small typo/comments fixed.
    [led.cfg, sensors.cfg]
2024-12-13 cleaned up some division of responsibilities for pin assignments and moved stuff out of the dumb semi-perm printer.cfg #*# storage area back into relevant sections to make it easier to just comment o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
    [bed.cfg, cartographer.cfg, fans.cfg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]
2024-12-13 Updated extruder and bed heater PIDs.
    [bed.cfg, printer.cfg, xol.cfg]
2024-12-14 Finished carto setup AT TEMP 90'C. Also, cleaned up z-hop during z-tilt to be a little higher than 2mm. Also, moved home to be Z=20mm. Finally, proved to myself that you CAN redefine sections / value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
    [bed.cfg, cartographer.cfg, motion.cfg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]
2024-12-14 LOTS of status updates, print_start and print_end fixes. timelapse enabled.
    [macros.cfg, status.cfg]
2024-12-15 Update HEAT SOAK routine to target chamber temp.
    [macros.cfg]
2024-12-15 Fixed some print outs (and math error on average chamber temp parenthesis issue), turned off heaters after heat soak.
    [bed.cfg, macros.cfg]
2024-12-15 More PRINT_START clean up and trying to take out LED effects.
    [led.cfg, macros.cfg, status.cfg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]
2024-12-15 Tweaked some print dumps and redundant status setting. Cleaned up PRINT_END
    [bed.cfg, macros.cfg, status.cfg]
2024-12-15 clean up heat_soak more. mostly cosmetic
    [macros.cfg]
2024-12-15 Fixed if clause error on print
    [macros.cfg]
2024-12-15 fixed chamber within 15% of bed
    [macros.cfg]
2024-12-15 Updated options to print_start to include bedmesh and priming checks.
    [macros.cfg]
2024-12-15 Fixed an issue where Orca sends PF dynamic settings via M106 Sxx without any Pyy. I was using that to set ALL 3 fans. Made no Pyy default to P0 and P99 be "all". Also updated print_start to use chamb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
    [fans.cfg, macros.cfg, xol.cfg]
2024-12-16 quite a few updates in print_start and draw purge line as well as putting in some pauses to try to help the MCU THB failures coming out of temperature_waits.
    [calibration_macros.cfg, fans.cfg, macros.cfg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]
2024-12-16 Added more to DRAW_PURGE_LINES and some of the print_start. Broke out to calibration_macros.cfg too for later to remove non-necessary macros.
    [calibration_macros.cfg, led.cfg, macros.cfg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]
2024-12-17 Updated motion maximums based on speed tests.
    [calibration_macros.cfg, macros.cfg, motion.cfg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]
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2024-12-18 Updated order of z-tilt and bedmesh to happen after bedmesh, but BEFORE chamber temp soak..
    [Manta.cfg, calibration_macros.cfg, cartographer.cfg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]
2024-12-18 Clean up print_start some more...took out led_effects and crowsnest installation to work on TTC. removed LED calls.
    [bed.cfg, fans.cfg, hardware.cfg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]
2024-12-18 Broke led.cfg out into just the hardware definition/connections and then created led_effects.cfg and th_led_effects.cfg that pull in from macros.cfg (if/when I re-enable led_effects).
    [hardware.cfg, led.cfg, led_effects.cfg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]
2024-12-19 Added Adaptive BedMesh to Print_Start. new input shaper runs. returned to Siboor default cycle_time for fans now that TTC not a problem. Added back crowsnest to see if it works.
    [fans.cfg, macros.cfg, status.cfg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]
2024-12-21 Updated input shaper (card table likely reason for double x hump) and changed LED default to "warm" up. Fixed issues with the load/unload filament.
    [led.cfg, macros.cfg, xol.cfg]
2024-12-22 Updated macros for better / safer homing order and checks.
    [Custom Siboor 350 XOL umbilical.stl, bed.cfg, fans.cfg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]
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2024-12-27 Rename AWD_350_Model_TMC5160_new.cfg to Siboor Trident AWD 350 TMC5160_new.cfg
    [Siboor Trident AWD 350 TMC5160_new.cfg]
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2024-12-28 Updated assets and added simultaneous definitions for Carto and EBB36 ADXL345 chips.
    [cartographer.cfg, hardware.cfg, macros.cfg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]
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2024-12-29 Update z-tilt to include a BED_MESH_CLEAR...followed by REHOME HOME
    [status.cfg]
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2024-12-30 Removed HOME_IF_NEEDED macro (not necessary with current G28 over-ride). Also, replaced most of the self calculated max/2 for x/y with the corrected (min+max)/2
    [macros.cfg, status.cfg]
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2024-12-30 Update description of G32 as well as finish Z HOME at 30
    [bed.cfg, status.cfg]
2024-12-30 Typo fixes in home
    [macros.cfg, status.cfg]
2025-01-01 Added moonraker.db backup JSON export for Fluidd settings
    [motion.cfg]
2025-01-03 Updated config changes (needed to fix CORS violation for Synology Docker Fluidd domain?)
    [printer.base.cfg]
2025-01-03 Pretty big rip up/move of code from STATUS and MACROS to the respective MOTION and BED for home and stuff. This required a lot of testing and learning for how many times you can (can't really) rename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
    [bed.cfg, macros.cfg, motion.cfg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]
2025-01-03 Few more fixes for z_tilt_adjust same way and fix malformed macro not allowing single parameter arguments like G-codes do (HOME Z for example)
    [bed.cfg, cartographer.cfg, macros.cfg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]
2025-01-03 one last fix to always leave head in center even if only homing X.
    [motion.cfg]
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2025-01-09 Update PRINT_START to wait on HE to 150'C before touch z-offset.
    [macros.cfg]
2025-01-09 Remove the 120'C HE settings/stage during chamber temps and just use 150'C for simplicity. This was more straight forward when I was stepping up during chamber soak, but when I moved bedmesh/z-tilt/t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
    [macros.cfg]
2025-01-09 Commented on the reasoning and long brutal work I did on trying to redefine G28 TWICE (once in motion and once again in Status).
    [motion.cfg]
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2025-01-20 Updated warning of SB is not actively developed.
    [stealthburner.cfg]
2025-01-20 Added Runout sensor switch to 4-to-1 filament hub block.
    [sensors.cfg]
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2025-01-22 Updated Print Start macro to ensure enough bed heating headroom to chamber temp criteria and updated Input Shaping
    [hardware.cfg, macros.cfg, sensors.cfg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]
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2025-01-27 Added in Obico settings/macros. Added in LED.cfg for just basic LED macro.
    [addins.cfg, led.cfg, macros.cfg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]
